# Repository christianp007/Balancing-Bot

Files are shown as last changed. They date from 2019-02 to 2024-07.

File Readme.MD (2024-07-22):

# Balancing-Bot
 A 3d printable balancing bot designed in Fusion360

Just another balancing robot... but with hair! :-)

The bot is using stepper motors, an accelerometer/gyro and a pid loop programmed in Arduino IDE for an AtMega328p.<br>
The bot can be controlled using a Bluetooth, i recommend the app 'Arduino Bluetooth RC Car' for Android (not tested with IPhone).

The source code and build instructions (german language only at the moment) are included in a PDF: [Build Instruktions](Balancing%20Bot%20instructions.pdf)<br>

Programming the HC-05 module with these instructions:<br>
(from https://www.instructables.com/Modify-The-HC-05-Bluetooth-Module-Defaults-Using-A/)<br>
set serial monitor in arduino ide to 9600 baud and connect<br>
AT+ORGL<br>
AT+VERSION?<br>
AT+NAME=Bot red<br>
AT+UART=57600,1,0<br>
AT+POLAR)1,0<br>

The code is structured this way it is as it was provided incomplete and had to be completed by the teams. Additionally it was my first arduino project (i'm a java programmer)...<br>

It was designed mostly in Fusion 360 and for the skind/hairs OpenSCAD.<br>
Fusion 360 couldn't handle the thousands of hairs, however rendering in openscad can take a few hours.

Bill of materials (BOM):<br>
3x stepper motor 14HS11-1004S (Nema 14 35x25x28mm with low inductance)<br>
3x stepper driver DRV8834 (this is a low voltage driver that works with 5V)<br>
1x Powerbank 'Powerad Slim 2'<br>
1x Bread Board 830 point<br>
1x Microcontroller ATMega328P-PU (preferably with Arduino Bootloader installed)<br>
1x HC-05 Bluetooth module<br>
1x Gyro MPU-9250<br>
1x 5V Speaker<br>
1x Micro USB adapter<br>
1x capacitor 220uF<br>
4x capacitor 100uF<br>
1x capacitor 10uF<br>
2x capacitor 10pF<br>
4x resistor 1 kOhm<br>
4x resistor 10 kOhm<br>
1x Pushbutton<br>
1x crystal 16 MHz<br>
(optional) Bluetooth Stick for your computer (upload Arduino sketches directly from arduino ide)<br>
some breadboard wires or cut and strip wires yourself<br>

Print Time: About 24 hours<br>
I used an Kossel XL and a 0.25mm nozzle<br>

Material: PLA<br>
The tire have to be printed in a flexible material (i used Ninjaflex), or you can print tires and wheels as one part in PLA.

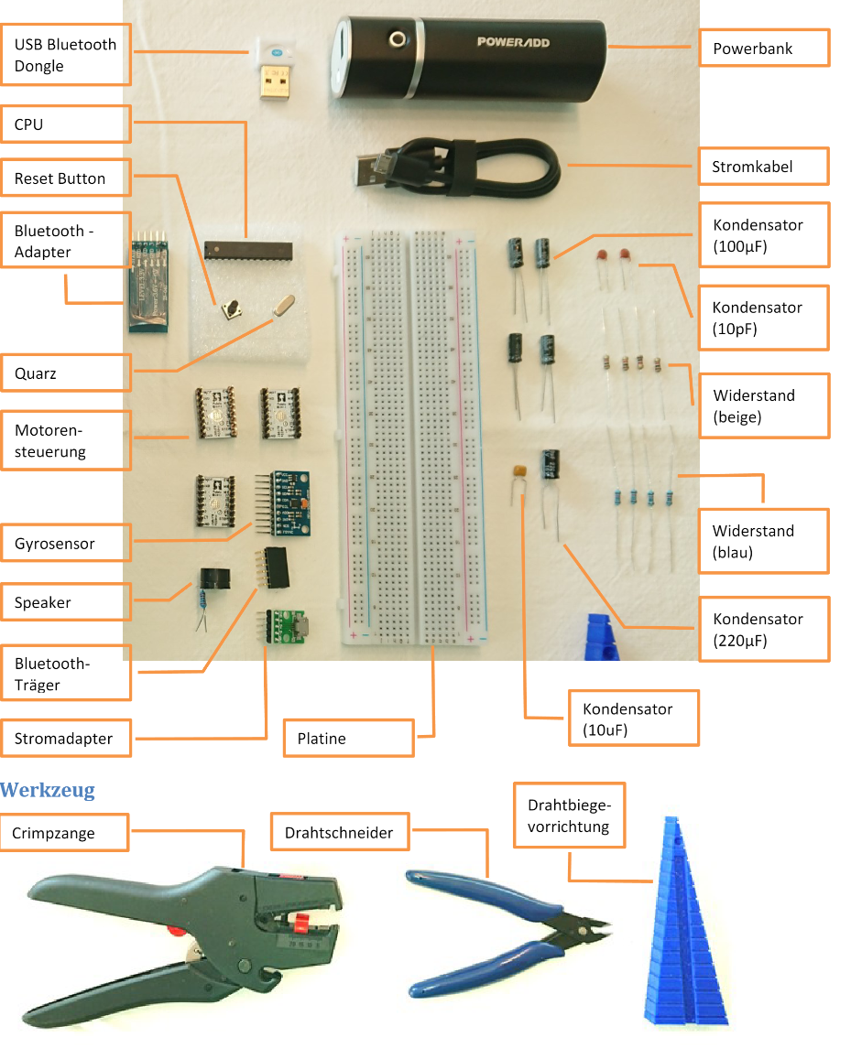
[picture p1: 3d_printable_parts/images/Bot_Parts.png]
Bot_Parts Bot Parts

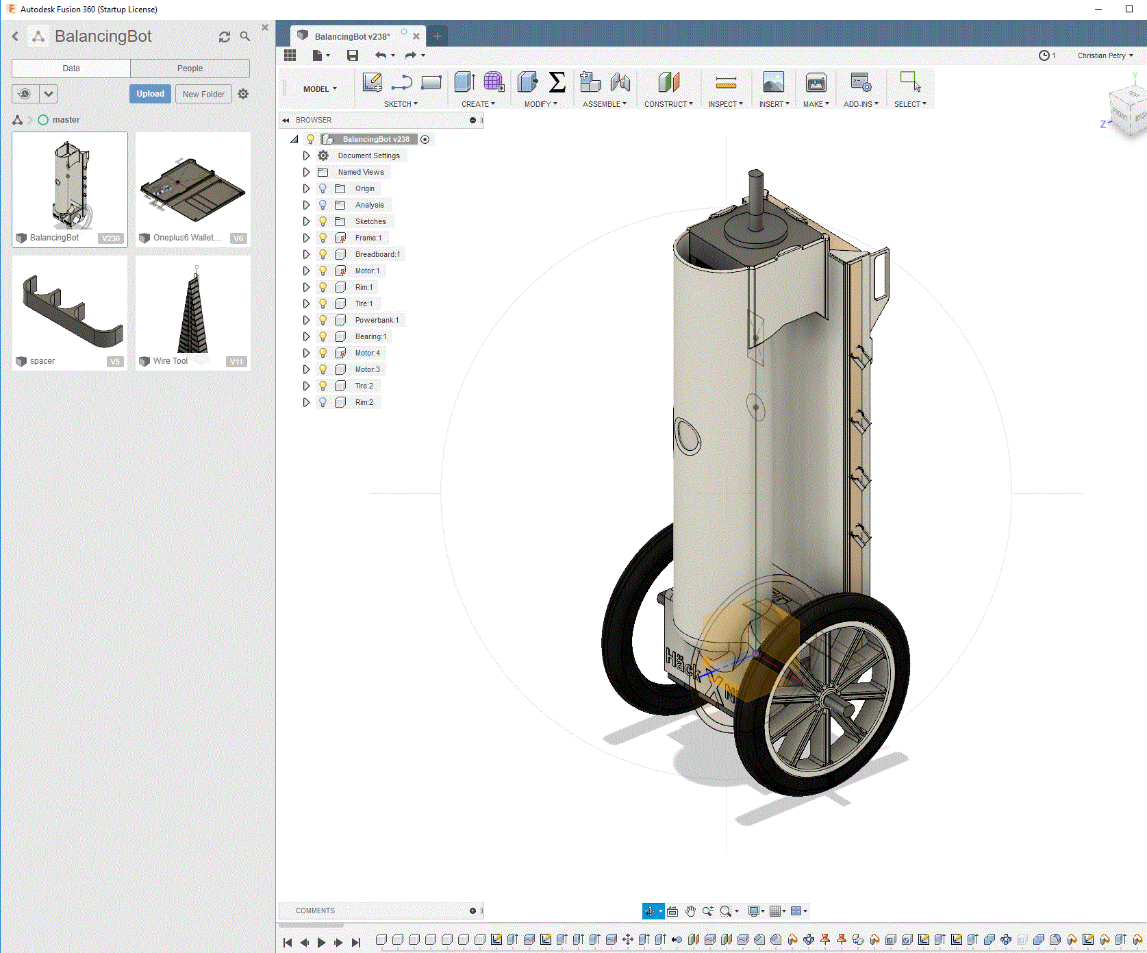
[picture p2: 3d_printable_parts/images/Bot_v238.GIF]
Bot_v238 Bot v238

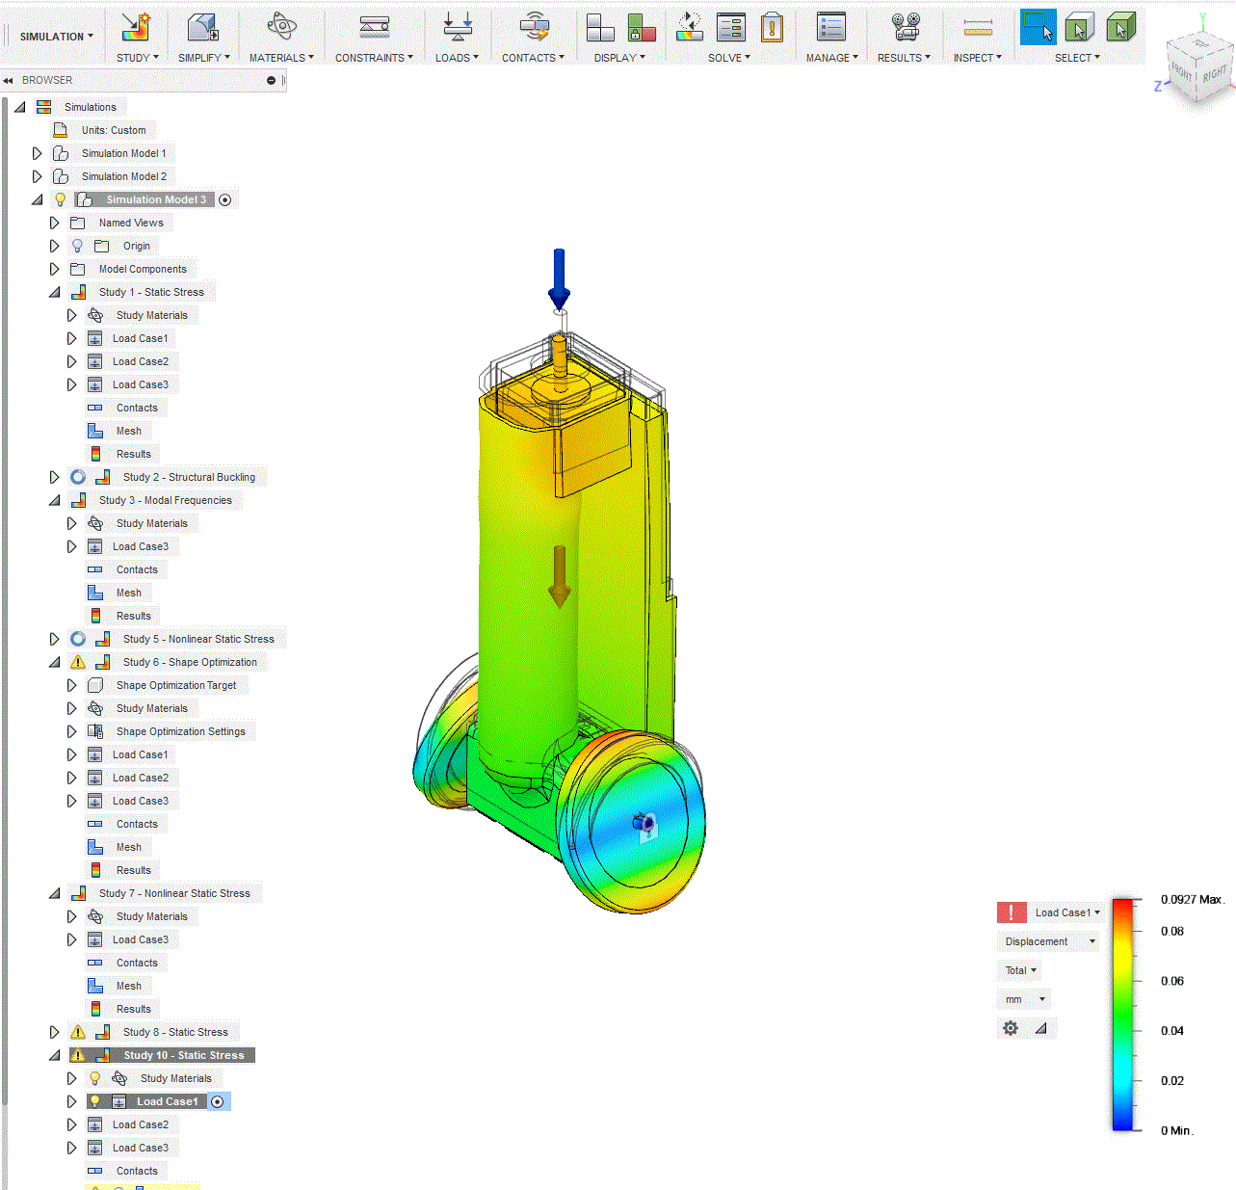
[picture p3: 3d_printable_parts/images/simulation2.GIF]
simulation2

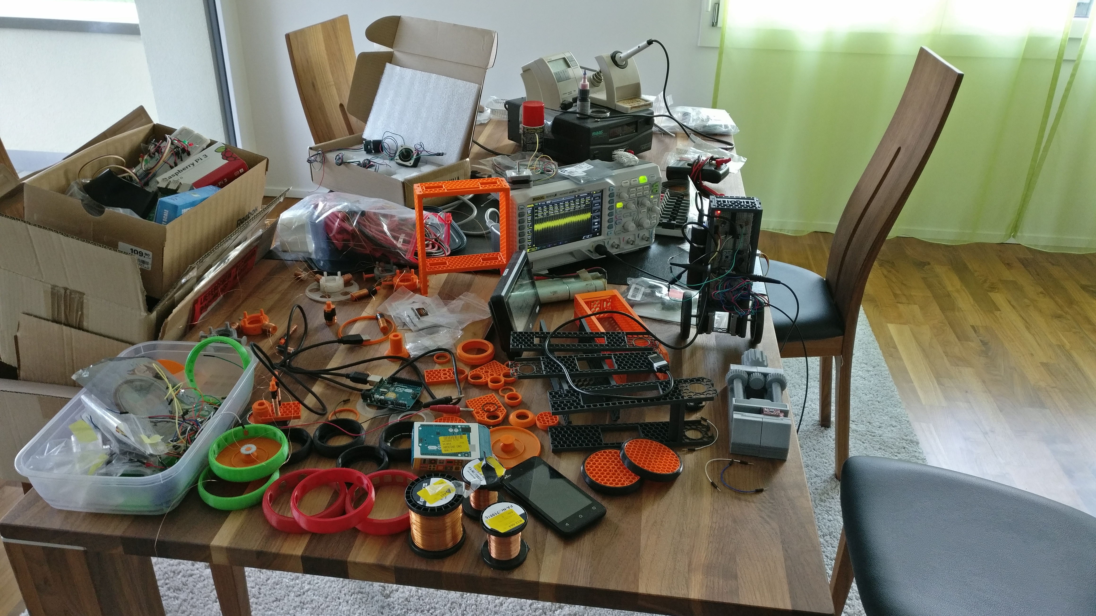
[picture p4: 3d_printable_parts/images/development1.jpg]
development1

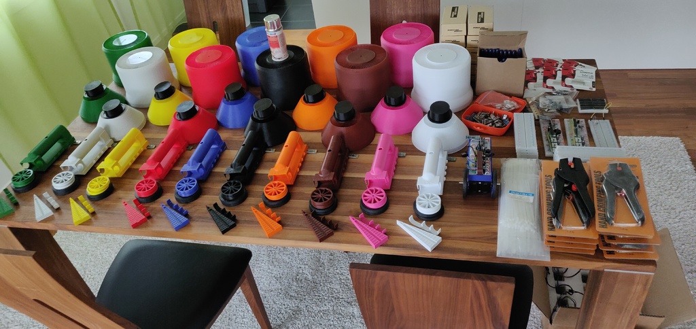
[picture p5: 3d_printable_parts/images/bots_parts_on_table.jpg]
bots_parts_on_table

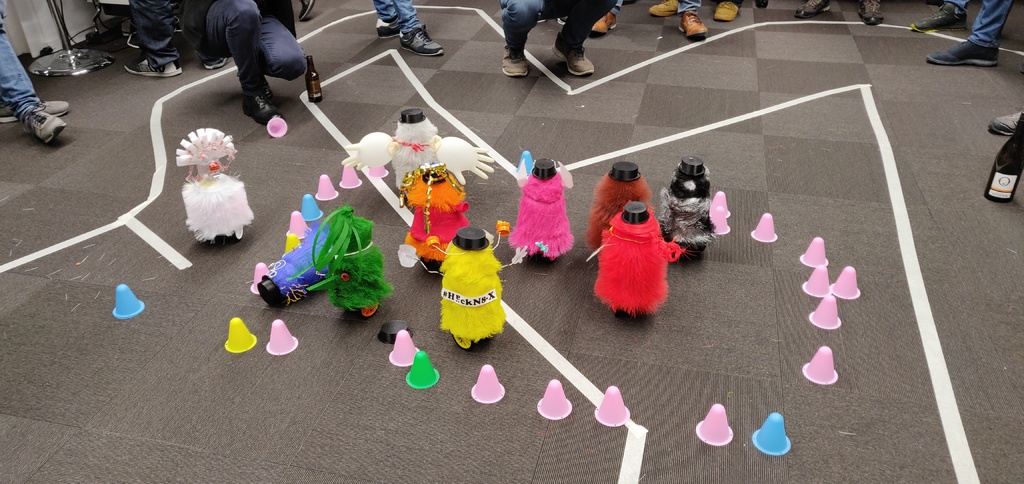
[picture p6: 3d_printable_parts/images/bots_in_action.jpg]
bots_in_action

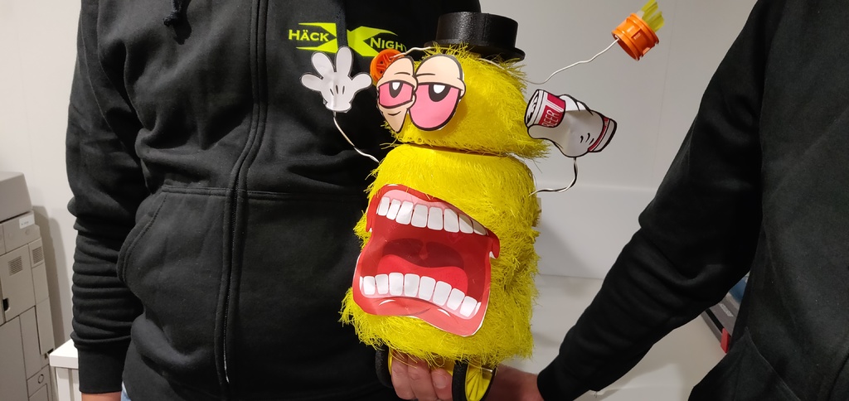
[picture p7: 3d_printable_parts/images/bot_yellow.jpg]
bot_yellow

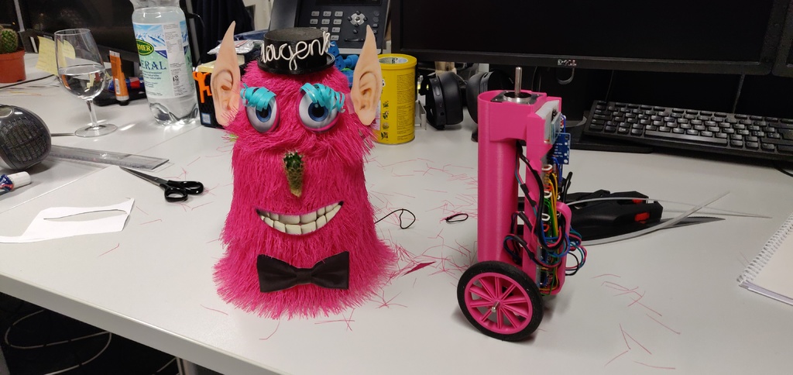
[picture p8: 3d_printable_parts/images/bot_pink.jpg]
bot_pink

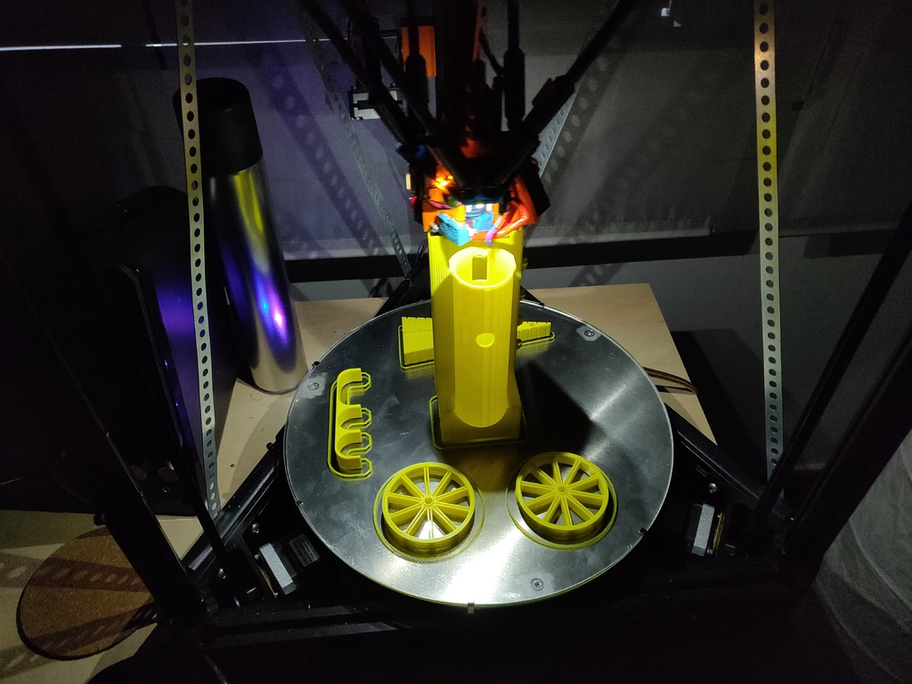
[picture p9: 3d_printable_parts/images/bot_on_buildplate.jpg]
bot_on_buildplate

hair

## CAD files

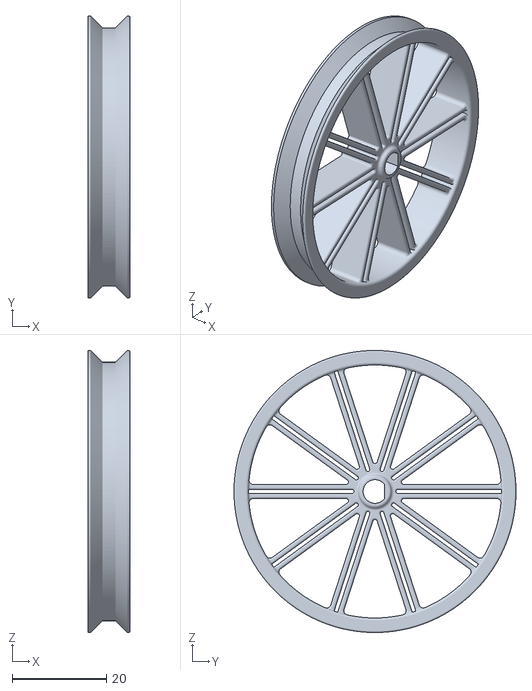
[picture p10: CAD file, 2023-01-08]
3d_printable_parts/RimV238.stl
9.00 x 60.0 x 60.0

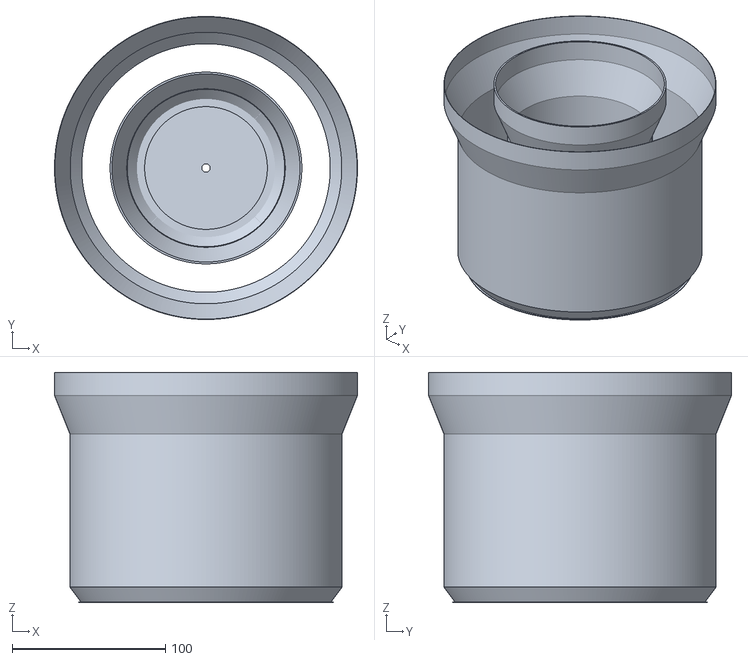
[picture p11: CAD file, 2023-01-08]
3d_printable_parts/balancing_bot_suiteV3__skin.stl
197.5 x 197.5 x 150.0

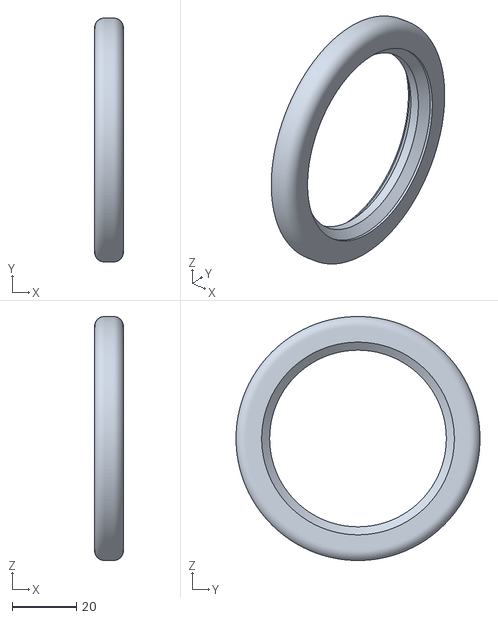
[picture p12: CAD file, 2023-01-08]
3d_printable_parts/TireV238.stl
9.00 x 76.0 x 76.0

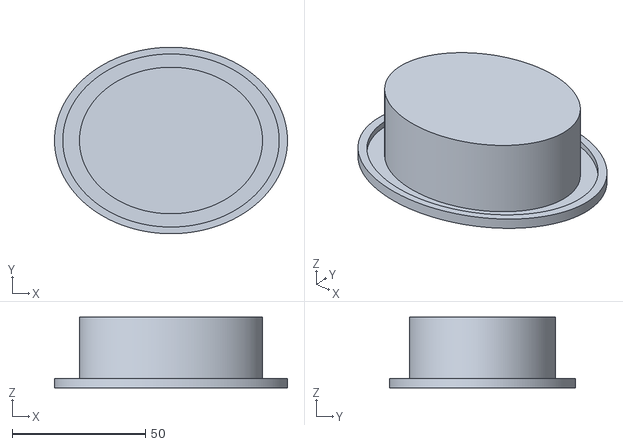
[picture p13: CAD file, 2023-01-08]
3d_printable_parts/balancing_bot_suiteV3__hat.stl
87.5 x 70.0 x 26.5

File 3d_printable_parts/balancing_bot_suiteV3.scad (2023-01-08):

OVERLAP = 0.001;
HAIRS_PER_LAYER = 100;
LAYER_SHIFT_DISTANCE = 0.2;

defaultHairLength = 36;
nozzleWidth = 0.27;
layerHeight = 0.20;
innerOverlap = 2.0*nozzleWidth;
outerOverlap = 0.5*nozzleWidth;
defaultWallThickness = 3*nozzleWidth;
topThickness = 4*layerHeight;

PART = "HAT"; // BODY_HAIR, BODY_SKIN, HEAD_HAIR, HEAD_SKIN, HAT

create();

module create(){
    if (PART == "BODY_HAIR"){
        $fn=50;
        hair(90,105,10,0);
        hair(105,105,5,10);
        hair(105,105,95,15);
        hair(105,125,25,110);
        hair(125,125,15,135);
    } else if (PART == "BODY_SKIN"){
        $fn=200;
        skin(90,105,10,0,1.5*defaultWallThickness);
        skin(105,105,5,10,1.5*defaultWallThickness);
        skin(105,105,95,15);
        skin(105,125,25,110);
        skin(125,125,15,135,1.5*defaultWallThickness);
        difference(){
            cylinder(d=90+OVERLAP, h=topThickness);
            translate([0,0,-OVERLAP/2])
            cylinder(d=5.5, h=topThickness+OVERLAP);
        }
        translate([0,0,topThickness])
        difference(){
            cylinder(d=90+OVERLAP, h=topThickness);
            translate([0,0,-OVERLAP/2])
            cylinder(d=80, h=topThickness+OVERLAP);
        }
        
        difference(){
            cylinder(d=90+2*defaultHairLength+4, h=2*layerHeight);
            translate([0,0,-OVERLAP/2])
            cylinder(d=90+2*defaultHairLength, h=2*layerHeight+OVERLAP);
        }
    } else if (PART == "HEAD_HAIR"){
        $fn=50;
        headDia = 91;
        hair(headDia,headDia,15,0);
        hair(headDia,20,headDia*1.15/2-1,15);
    } else if(PART == "HEAD_SKIN"){
        $fn=200;
        headDia = 91;
        
        difference(){
            union(){
                translate([0,0,15])
                scale([1,1,1.15])
                difference(){
                    sphere(headDia/2);
                    translate([-headDia/2,-headDia/2,-headDia])
                    cube(headDia+OVERLAP);
                    
                    translate([-headDia/2,-headDia/2,headDia/2-1])
                    cube(headDia+OVERLAP);
                }
                    
                translate([0,0,0])
                cylinder(d=15, h=headDia/2*1.15+15-1.5+24, $fn=6);
                
                cylinder(d=headDia,h=15);
            }
            
            cylinder(d=5.2, h=100, center=true);
            cylinder(d=5.6, h=0.6, center=true);
        }
        
        difference(){
            cylinder(d=90+2*defaultHairLength+4, h=2*layerHeight);
            translate([0,0,-OVERLAP/2])
            cylinder(d=90+2*defaultHairLength, h=2*layerHeight+OVERLAP);
        }
        
        skin(headDia,headDia,15,0);
        skin(headDia,20,headDia*1.15/2-1.2,15);
    } else if (PART == "HAT"){
        $fn=200;
        difference(){
            scale([1.25,1,1])
            {
                cylinder(d=70, h=1.5);
                
                translate([0,0,1.5-OVERLAP])
                difference(){
                    cylinder(d=70, h=2);
                    cylinder(d=65, h=2+OVERLAP);
                }
                
                translate([0,0,1.5-OVERLAP])
                cylinder(d=55, h=25);
            }
            
            translate([0,0,0])
            cylinder(d=15.9, h=25.2, $fn=6);
            
            translate([0,0,0])
            cylinder(d=16.2, h=0.8, $fn=6);
            
            translate([0,0,-OVERLAP])
            cylinder(d=16.5, h=0.4, $fn=6);
        }
    }
}

module hair(innerDiaStart, innerDiaEnd, height, startHeight, hairLength=defaultHairLength, layerShiftStart=0, wallThickness=defaultWallThickness){
    color("blue")    
    for(i=[1:height]){
        dia = innerDiaStart - 2*innerOverlap + (innerDiaEnd-innerDiaStart)*i/height;
        for (j=[0:360/HAIRS_PER_LAYER:359.9]){
            rotate([0,0,j+(layerShiftStart+i*360/HAIRS_PER_LAYER*LAYER_SHIFT_DISTANCE)])
            translate([dia/2,-nozzleWidth/2,startHeight+i])
            cube([hairLength+innerOverlap+outerOverlap,nozzleWidth,layerHeight]);
            //rotate([-90,0,90])
            //cylinder(h=hairLength,d=nozzleWidth,center=true);
        }
    }
}

module skin(innerDiaStart, innerDiaEnd, height, startHeight, wallThickness=defaultWallThickness){
    translate([0,0,startHeight])
    difference(){
        cylinder(d1=innerDiaStart, d2=innerDiaEnd, h=height);
        translate([0,0,-OVERLAP/2])
        cylinder(d1=innerDiaStart-2*wallThickness, d2=
innerDiaEnd-2*wallThickness, h=height+OVERLAP);
    }
    
    translate([0,0,startHeight])
    difference(){
        cylinder(d1=innerDiaStart+2*defaultHairLength+2*nozzleWidth, d2=innerDiaEnd+2*defaultHairLength+2*nozzleWidth, h=height);
        translate([0,0,-OVERLAP/2])
        cylinder(d1=innerDiaStart+2*defaultHairLength, d2=
innerDiaEnd+2*defaultHairLength, h=height+OVERLAP);
    }
}

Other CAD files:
3d_printable_parts/spacer v5.f3d

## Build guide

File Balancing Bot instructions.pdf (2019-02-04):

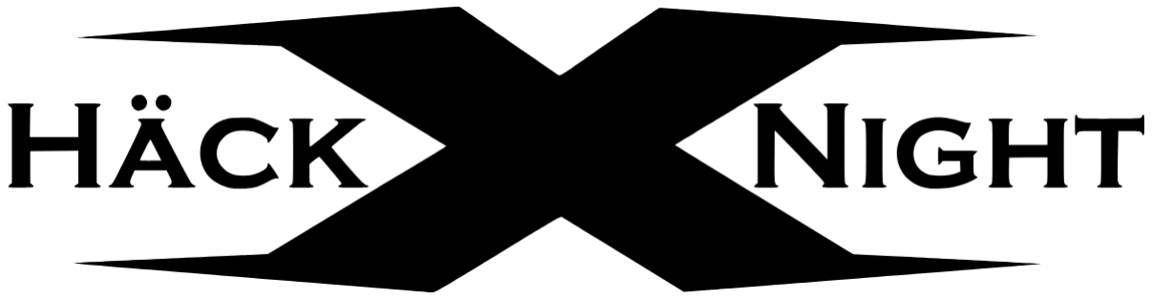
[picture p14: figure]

# Bauanleitung Balancing Bot

### Tipps zum Zusammenbau / Best practices

- Benutze die Drahtbiegevorrichtung, um die (meisten) Drähte auf die gewünschte Länge zu biegen und zu schneiden. Für die längeren Drähte brauchst du ein Lineal.
- Benutze die Drahtbiegevorrichtung auch zum Kürzen von Kondensatoren und Widerständen (in die Vertiefung im oberen Teil einsetzen und auf der Rückseite abschneiden).
- Spare Zeit, indem dein Team gleichzeitig die Drähte vorbereitet und die elektrischen Komponenten auf der Platine installiert.
- Lese jeden Schritt in dieser Anleitung sorgfältig durch. Achte insbesondere auf die korrekte Polung und vergleiche deine Arbeit mit den Bildern.
- Lasse nach jedem Arbeitsschritt die Platine durch eine zweite Person reviewen. Fehlerhafte Verbindungen sind im Nachhinein extrem schwierig zu finden!
- Keine Kabel und Komponenten ein- oder ausstecken, wenn die PowerBank angeschlossen ist! PowerBank immer vorher trennen!

### Übersicht

### Bot Bauteile

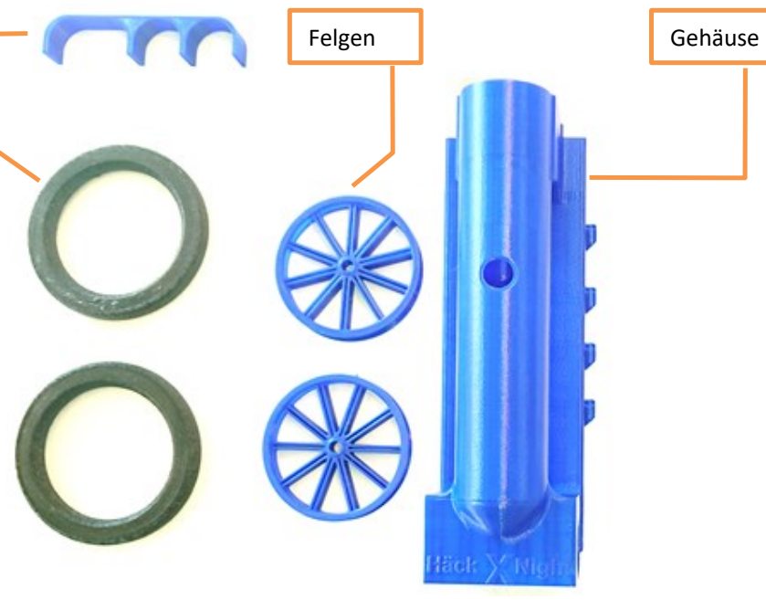
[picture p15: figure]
Felgen; Gehäuse

Schutzkappe

Reifen

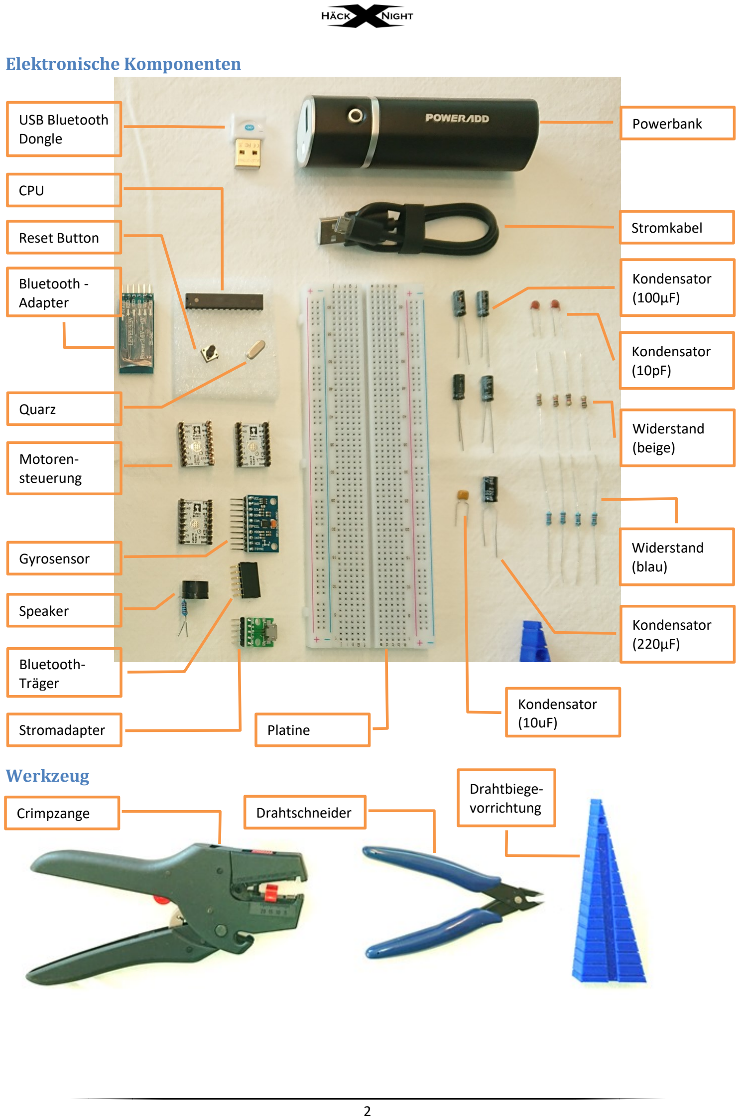
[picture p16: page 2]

### Elektronische Komponenten

### Werkzeug

USB Bluetooth
Dongle

Powerbank

CPU

Reset Button

Bluetooth -
Adapter

Stromkabel

Quarz

Motorensteuerung

Gyrosensor

Speaker

Kondensator
(100µF)

Kondensator
(10pF)

Widerstand
(beige)

Widerstand
(blau)

Kondensator
(220µF)
Bluetooth-Träger
Stromadapter | Platine

Kondensator
(10uF)
Crimpzange | Drahtschneider

Drahtbiegevorrichtung

### Vorbereitung

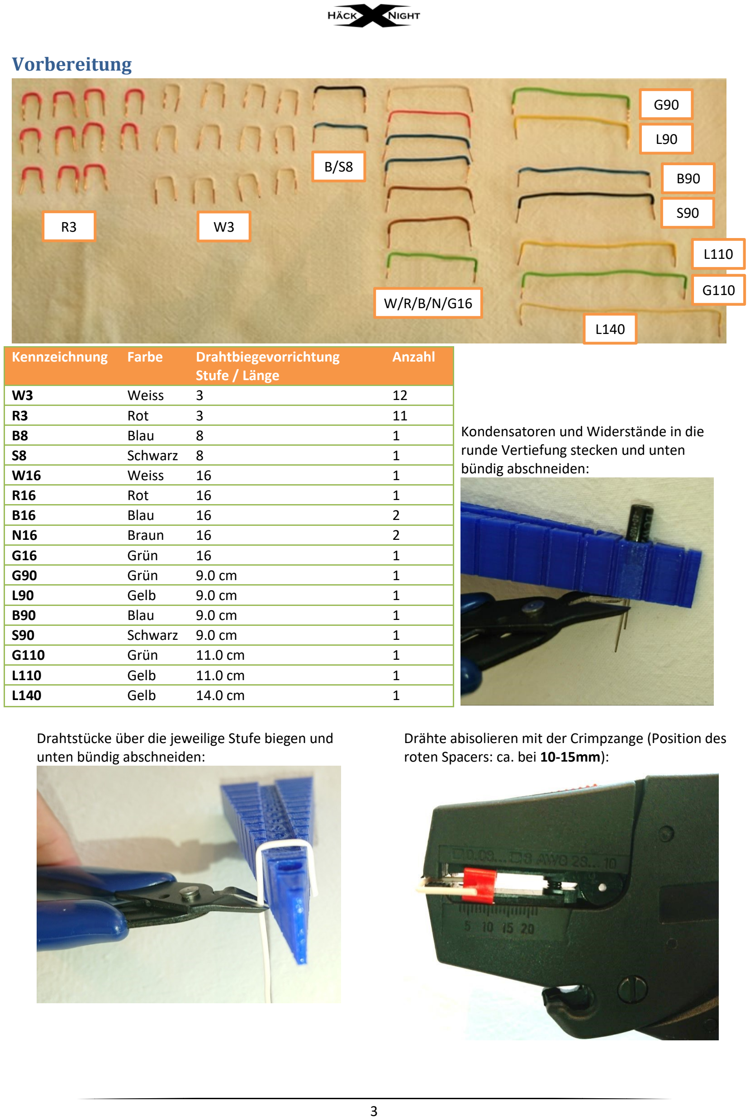
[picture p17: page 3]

Kennzeichnung | Farbe | Drahtbiegevorrichtung Stufe / Länge

Anzahl

Kondensatoren und Widerstände in die runde Vertiefung stecken und unten bündig abschneiden:

W3 | Weiss | 3 | 12
R3 | Rot | 3 | 11
B8 | Blau | 8 | 1
S8 | Schwarz 8 | 1
W16 | Weiss | 16 | 1
R16 | Rot | 16 | 1
B16 | Blau | 16 | 2
N16 | Braun | 16 | 2
G16 | Grün | 16 | 1
G90 | Grün | 9.0 cm | 1
L90 | Gelb | 9.0 cm | 1
B90 | Blau | 9.0 cm | 1
S90 | Schwarz 9.0 cm | 1
G110 | Grün | 11.0 cm | 1
L110 | Gelb | 11.0 cm | 1
L140 | Gelb | 14.0 cm | 1

Drahtstücke über die jeweilige Stufe biegen und
unten bündig abschneiden:
| | | Drähte abisolieren mit der Crimpzange (Position des roten Spacers: ca. bei 10-15mm):
R3 | W3

B/S8

W/R/B/N/G16

G90

L90

B90

S90

L110

G110

L140

### Bauanleitung

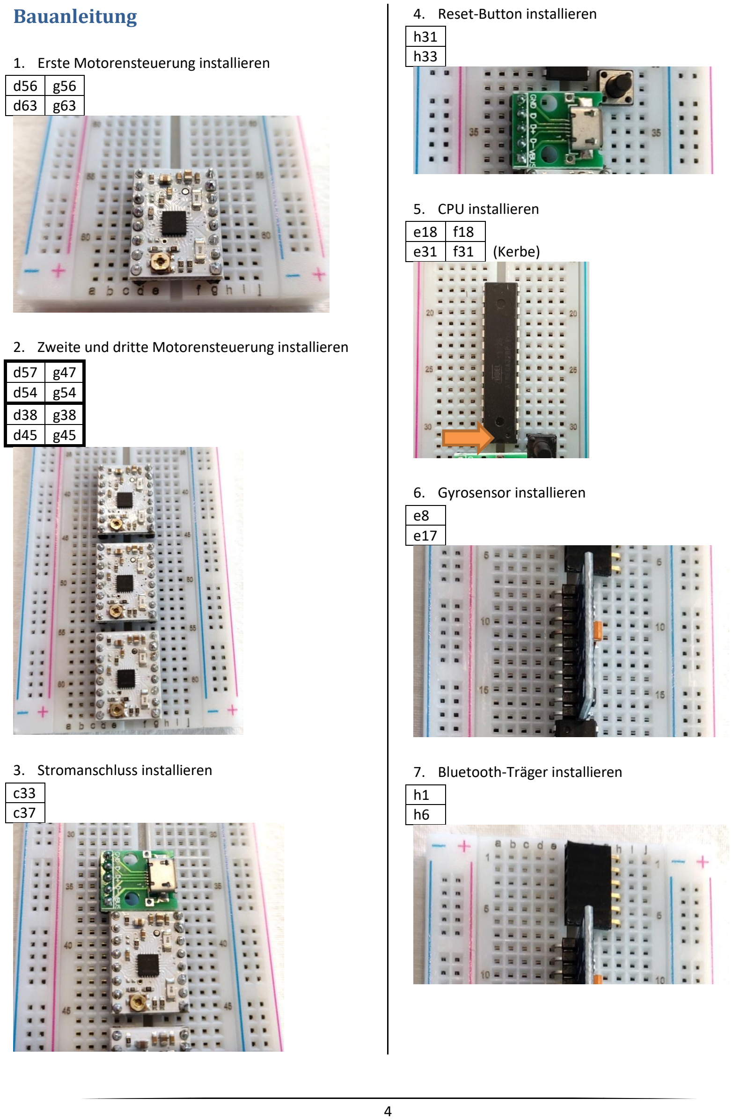
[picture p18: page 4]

1. Erste Motorensteuerung installieren
d56 | g56
d63 | g63
2. Zweite und dritte Motorensteuerung installieren
d57 | g47
d54 | g54
d38 | g38
d45 | g45
3. Stromanschluss installieren c33
c37
4. Reset-Button installieren h31
h33
5. CPU installieren
e18 | f18
e31 | f31 | (Kerbe)
6. Gyrosensor installieren e8
e17
7. Bluetooth-Träger installieren h1
h6

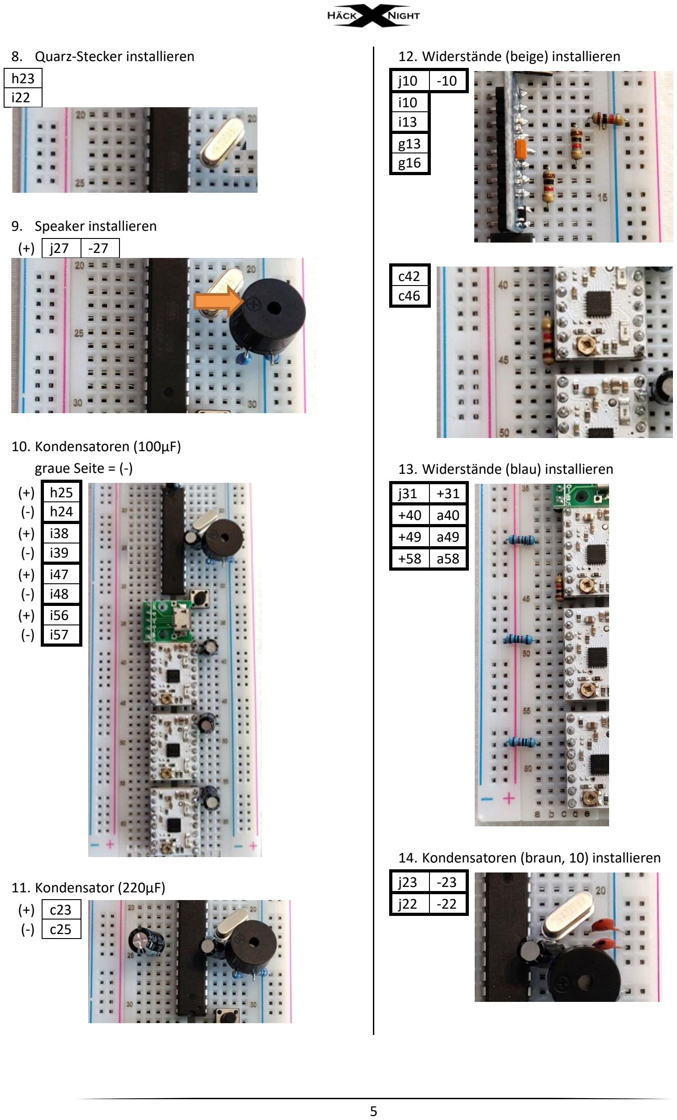
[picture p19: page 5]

8. Quarz-Stecker installieren h23
i22
9. Speaker installieren
(+) | j27 | -27
10. Kondensatoren (100µF)
graue Seite = (-)
(+) | h25
(-) | h24
(+) | i38
(-) | i39
(+) | i47
(-) | i48
(+) | i56
(-) | i57
11. Kondensator (220µF)
(+) | c23
(-) | c25
12. Widerstände (beige) installieren j10 -10
i10
i13
g13
g16

c42
c46
13. Widerstände (blau) installieren
j31 | +31
+40 | a40
+49 | a49
+58 | a58
14. Kondensatoren (braun, 10) installieren
j23 | -23
j22 | -22

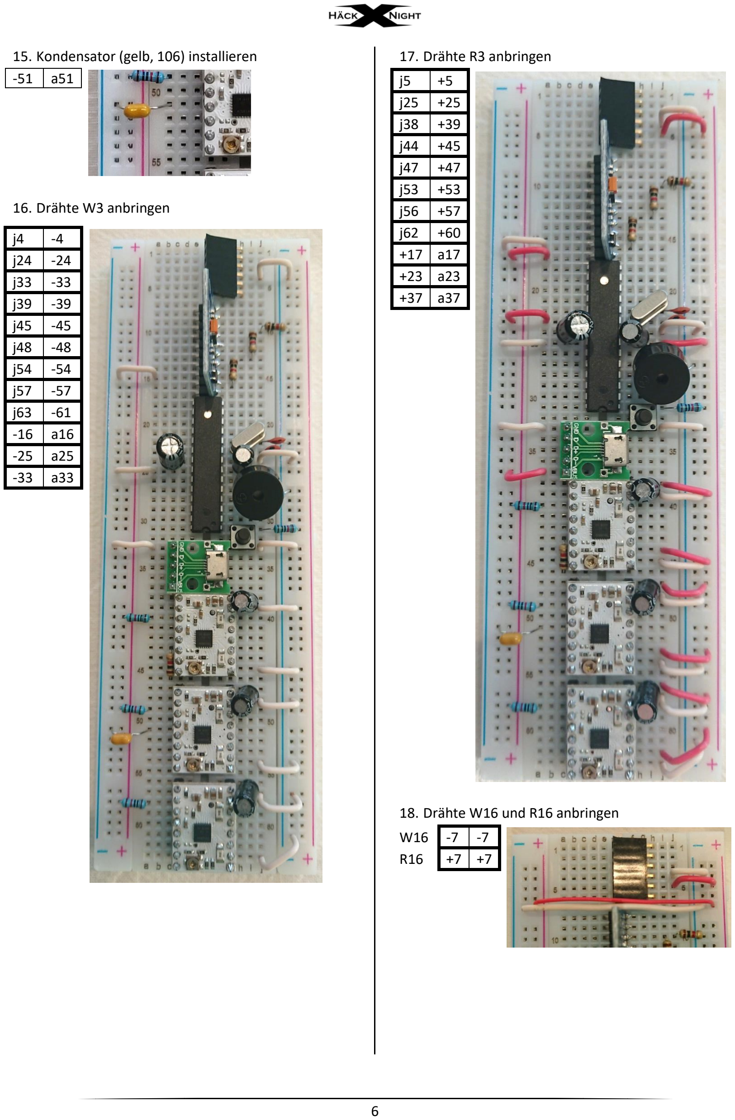
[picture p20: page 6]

15. Kondensator (gelb, 106) installieren -51 a51
16. Drähte W3 anbringen
17. Drähte R3 anbringen
j5 | +5
j25 | +25
j38 | +39
j44 | +45
j47 | +47
j53 | +53
j56 | +57
j62 | +60
+17 | a17
+23 | a23
+37 | a37
18. Drähte W16 und R16 anbringen
W16 | -7 | -7
R16 | +7 | +7
j4 | -4
j24 | -24
j33 | -33
j39 | -39
j45 | -45
j48 | -48
j54 | -54
j57 | -57
j63 | -61
-16 | a16
-25 | a25
-33 | a33

19. Draht S8 anbringen
i2
h13

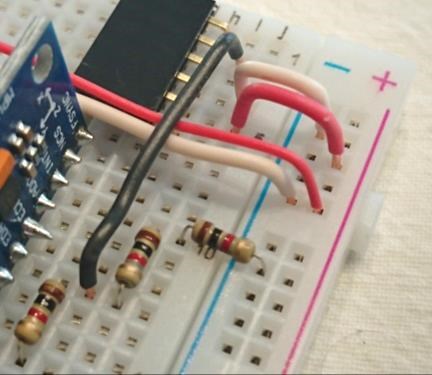
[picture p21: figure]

20. Draht B90 anbringen
(evtl. Speaker dafür entfernen) i3
j30

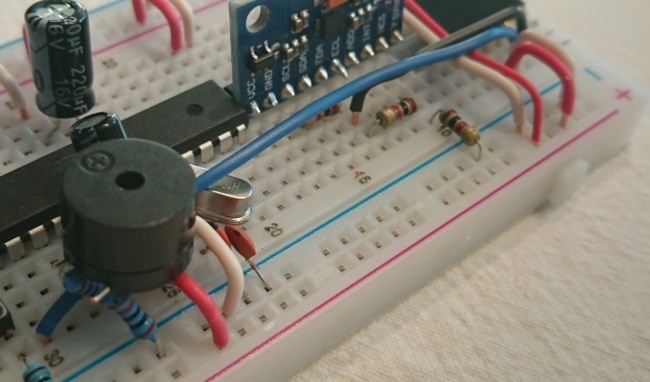
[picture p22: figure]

21. Drähte N16 anbringen
d14 | h16
d30 | g29

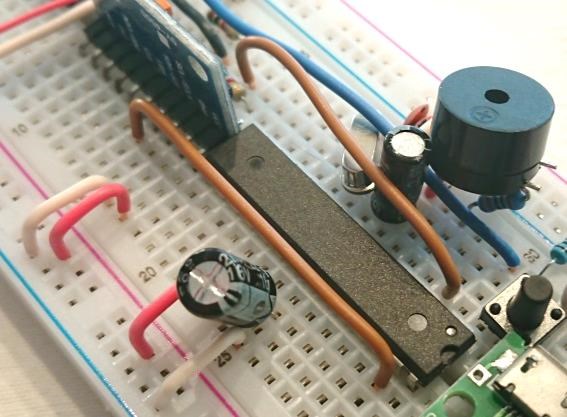
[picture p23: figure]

22. Drähte B16 anbringen
23. Draht B8 anbringen
24. Draht S90 anbringen
b18
b46

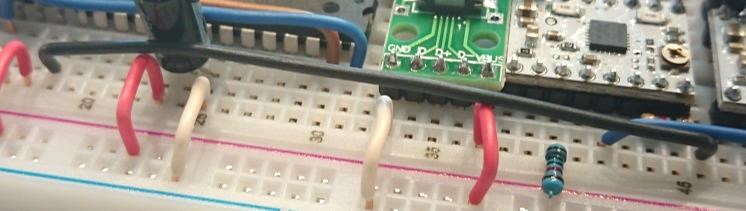
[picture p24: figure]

25. Drähte L90 / L110 / L140 anbringen L90 L110 L140
b20 | b21 | b22
b44 | b53 | b62

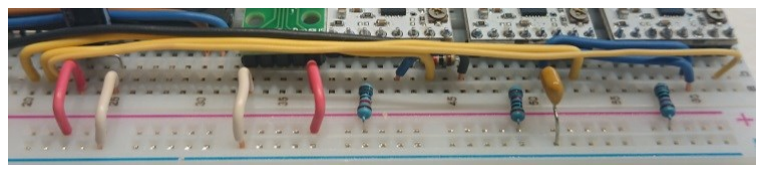
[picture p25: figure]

26. Drähte G16 / G90 / G110 anbringen G16 G90 G110
a27 | a28 | a29
a45 | a54 | a63

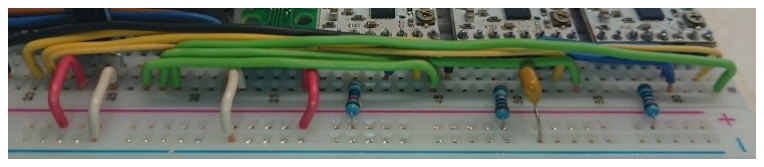
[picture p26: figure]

Die Platine ist nun (vorerst) fertig und bereit für den Einbau in den Bot! Ach ja, der Bot muss ja auch noch vorbereitet werden…

d15 | b42
d31 | a60

b51
b60

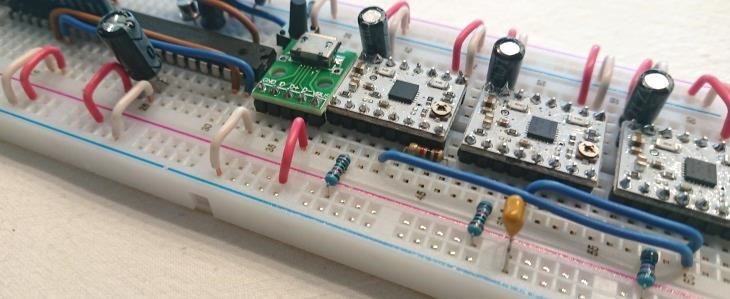
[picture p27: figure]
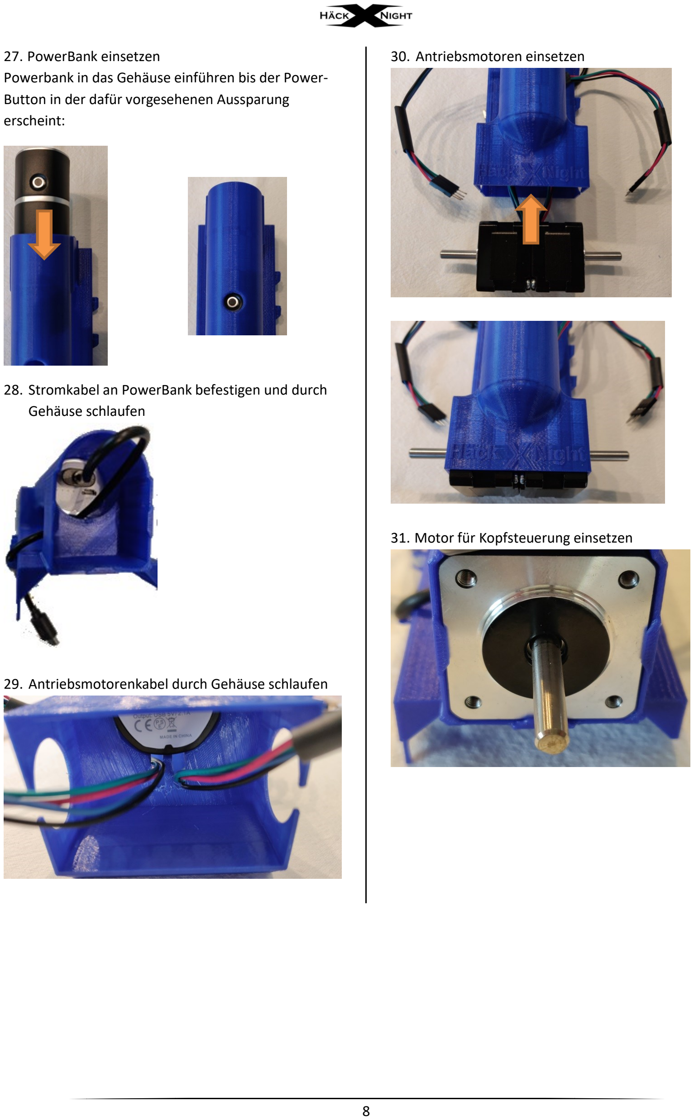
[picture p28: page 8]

27. PowerBank einsetzen
Powerbank in das Gehäuse einführen bis der Power-Button in der dafür vorgesehenen Aussparung erscheint:
28. Stromkabel an PowerBank befestigen und durch Gehäuse schlaufen
29. Antriebsmotorenkabel durch Gehäuse schlaufen
30. Antriebsmotoren einsetzen
31. Motor für Kopfsteuerung einsetzen

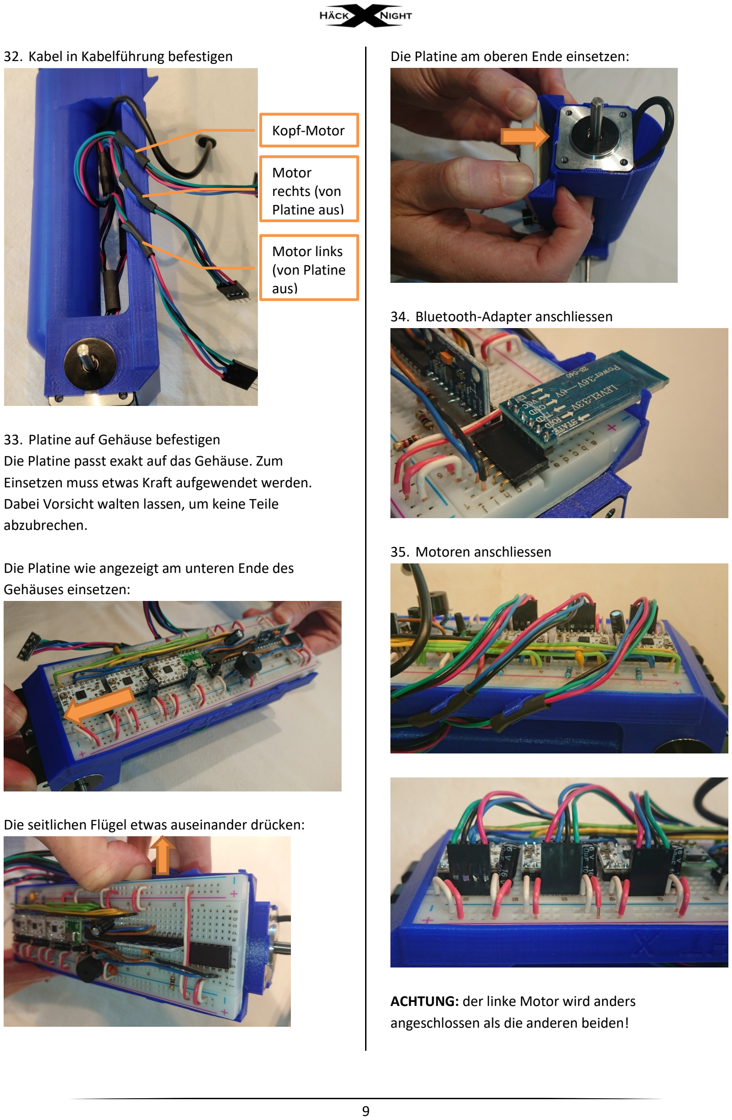
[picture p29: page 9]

32. Kabel in Kabelführung befestigen
33. Platine auf Gehäuse befestigen
Die Platine passt exakt auf das Gehäuse. Zum Einsetzen muss etwas Kraft aufgewendet werden. Dabei Vorsicht walten lassen, um keine Teile abzubrechen.

Die Platine wie angezeigt am unteren Ende des Gehäuses einsetzen:

Die seitlichen Flügel etwas auseinander drücken:

Die Platine am oberen Ende einsetzen:

34. Bluetooth-Adapter anschliessen
35. Motoren anschliessen

ACHTUNG: der linke Motor wird anders angeschlossen als die anderen beiden!

Kopf-Motor

Motor
rechts (von
Platine aus)

Motor links
(von Platine
aus)

36. PowerBank an Stromversorgung anschliessen

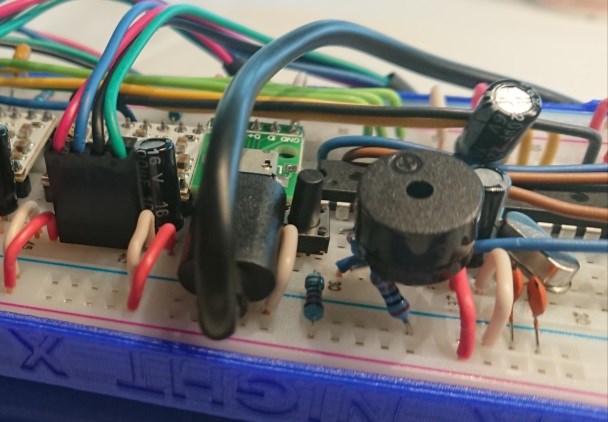
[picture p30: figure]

37. Schutzkappe aufstecken (bissl fummelig)

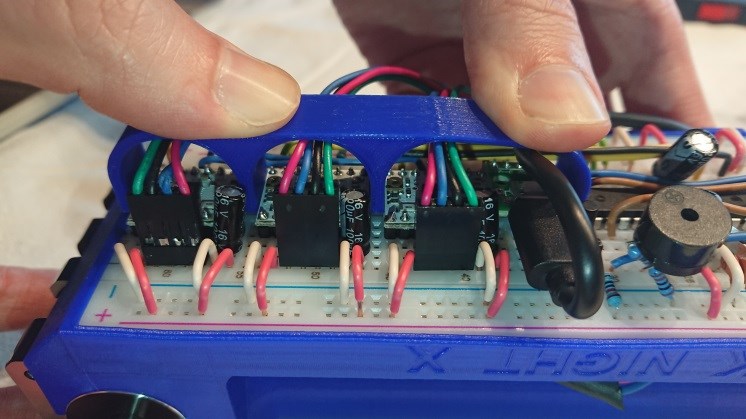
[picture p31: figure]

38. Pneus montieren

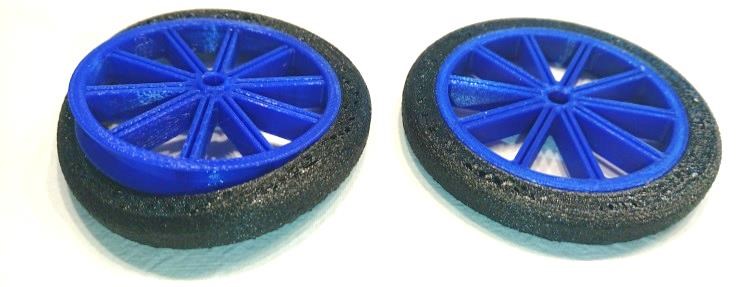
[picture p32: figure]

39. Reifen auf Motorenachsen aufsetzen
Auf zwei Punkte achten:
- Die Achse ist auf einer Seite etwas abgeflacht; ebenso das Loch in den Radspeichen
- Das Rad muss mit der Ausbuchtung nach aussen montiert werden:

Gratulation, ihr habt es geschafft!

Nun noch überprüfen, ob auch alles richtig eingesteckt und verdrahtet ist...

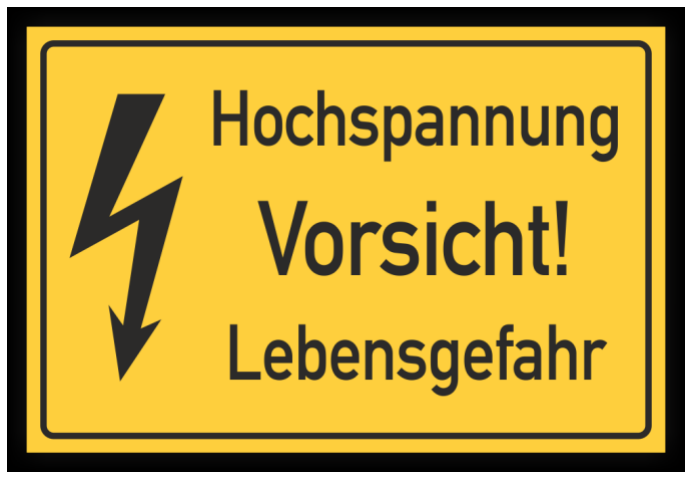
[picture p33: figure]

Keine Kabel und Komponenten ein- oder ausstecken, solange die PowerBank angeschlossen ist!

PowerBank immer vorher ausschalten und ausstecken!

Funktionstest:
1. PowerBank einschalten (ca. 3 Sekunden gedrückt halten. Sobald Bluetooth-Adapter blinkt und Räder etwas blockieren, ist Strom drauf)
2. Willkommens-Musik geniessen
3. Bot senkrecht hinstellen und solange (sanft) fixiert halten bis er von selbst balanciert

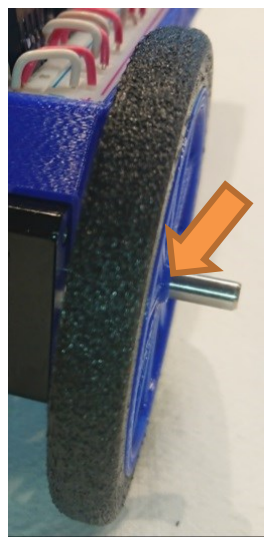
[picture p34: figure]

Wenn der Bot hinfällt oder durchdreht:
- Bot flach auf den Boden legen
- Warten bis er sich beruhigt hat, oder Reset-Button betätigen
- Bot wieder senkrecht hinstellen bis er von selbst balanciert

### Entwicklungsumgebung einrichten

Hinweis: benötigt zwingend eine Windows-Umgebung!

1. USB-Stick an Laptop oder PC anschliessen
2. ArduinoIDE starten von X:\arduino-1.8.7\arduino.exe
3. Tools -> Board -> „Arduino Duemilanove or Diecimila“ auswählen
4. Tools -> Processor -> „ATmega328P“ auswählen
5. Tools -> Programmer -> „AVRISP mkll“ auswählen
6. File -> Preferences -> Show verbose output during: | compilation | upload
7. File -> Open und folgende Datei öffnen: X:\balancingRobotV3\balancingRobotV3.ino
8. Tools -> Port -> angezeigte Ports merken (damit man nachher weiss, welche Ports NICHT zum Bot gehören)
9. Bot einschalten
10. Bluetooth einrichten:
a. Falls auf PC oder Laptop Bluetooth verfügbar ist: Bluetooth aktivieren
b. Falls auf PC oder Laptop kein Bluetooth verfügbar: Bluetooth-Dongle anschliessen
11. Bluetooth Einstellungen öffnen
12. Neues Bluetooth-Gerät hinzufügen und nach Gerät Bot {Color} suchen, wobei {Color} deiner Team-Farbe

entspricht

13. Pin eingeben: 1234

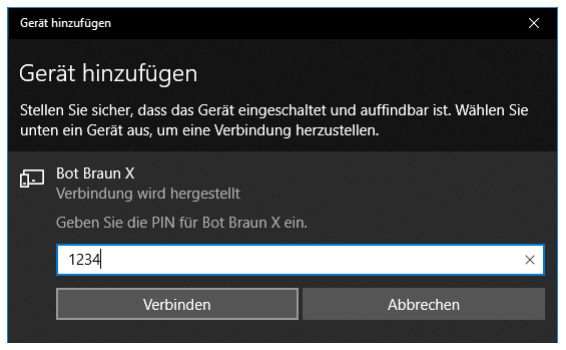
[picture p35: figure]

14. In der ArduinoIDE unter Tools -> Port den neuen Port auswählen. Evtl. IDE dazu neu starten.

Um das Projekt zu kompilieren: Ctrl + R drücken
- Fehler werden in roter Schrift in die Konsole geschrieben; zudem wird der Cursor an die Position des letzten Fehlers gesetzt.

Um das Projekt auf den Bot zu laden:
1. Reset-Button auf Bot gedrückt halten und das blinkende rote Licht am Bluetooth-Modul beobachten.
2. Ctrl + U drücken.
3. Reset-Button solange gedrückt halten, bis das rote Licht am Bluetooth-Modul unregelmässig wird. Dann Reset-Button sofort loslassen.
4. Upload wird durch einen Fortschrittsbalken (###...) in der Konsole angezeigt.
5. Wenn der Upload funktioniert hat, wird die Software auf dem Bot automatisch neu gestartet, und die Startmusik ertönt.

### Smartphone App einrichten

1. App von Google Play Store herunterladen: https://play.google.com/store/apps/details?id=braulio.calle.bluetoothRCcontroller

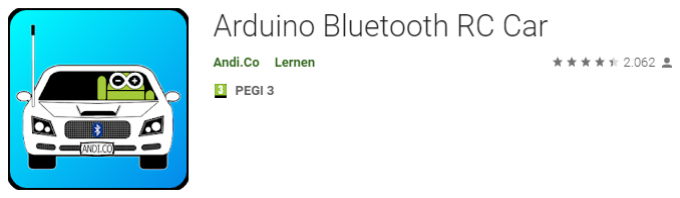
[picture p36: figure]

2. Bluetooth-Kopplung des Bots mit dem PC beenden (Bluetooth auf PC deaktivieren)
3. Bluetooth auf Handy aktivieren und mit Bot {Color} verbinden (Pin: 1234)
4. Wenn die Kopplung erfolgreich war, App starten
5. Einstellungen -> Mit Car verbinden -> Bot {Color} auswählen
6. Sobald das Statuslicht oben links grün leuchtet, kann mit dem Bot herumgekurvt werden (vorausgesetzt, ihr habt die Software auf dem Arduino entsprechend erweitert… )

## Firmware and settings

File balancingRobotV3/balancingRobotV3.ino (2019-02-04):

#include "balancingRobotV3.h"
#include "melody.h"

// --------------------- START custom settings ---------------------
const float INITIAL_TARGET_ANGLE = 2.5; // approximation of the angle at which the bot stands still
const float STARTUP_ANGLE_TOLERANCE = 3.0; // the acceptable range of angle error for start balancing
const float TIPOVER_ANGLE_OFFSET = 35; // stop motors if bot has tipped over
const float MAX_ACCELLERATION = 200.0; // maximum acceleration in steps per second per loop iteration
const float COMPLEMENTARY_FILTER_GYRO_COEFFICIENT = 0.999; // how much to use gyro value compared to accerelometer value
// ---------------------  END custom settings  ---------------------

// --------------------- START PID settings ---------------------
// pid for controlling angle
const float PID_ANGLE_P_GAIN = 6; // proportional pid gain
const float PID_ANGLE_I_GAIN = 0.05; // integral pid gain
const float PID_ANGLE_D_GAIN = -250; // differential pid gain
const float PID_ANGLE_I_MAX = 20; // limit for integral pid
const float PID_ANGLE_D_MAX = 20; // limit for differential pid

// pid for controlling speed
const float PID_SPEED_P_GAIN = 13.0;
const float PID_SPEED_I_GAIN = 0.01;
const float PID_SPEED_D_GAIN = 0;
const float PID_SPEED_I_MAX = 50000;
const float PID_SPEED_D_MAX = 10000;

// pid for controlling position
const float PID_POSITION_P_GAIN = -5;
const float PID_POSITION_I_GAIN = 0;
const float PID_POSITION_D_GAIN = 0;
const float PID_POSITION_I_MAX = 20;
const float PID_POSITION_D_MAX = 20;
// --------------------- END PID settings ---------------------

unsigned long currentTime = millis();

// --------------------- START music variables  ---------------
boolean playMusicModeActive = false;
int lastMusicTone = -1;
unsigned long lastMusicTime = 0;
int *balancing_melody = MELODY_PIRATE_CARIBBEAN;
int balancing_melody_size = sizeof(MELODY_PIRATE_CARIBBEAN)/sizeof(int);
// ---------------------- END music variables  ----------------

int count = 0;
void debugLoop(){
  if (count++ >= 50){
    count = 0;
    debugOutput();
  }
}

void debugOutput(){
    /* Use this to debug! 
     * don't do any computational intesive stuff as this will affect the balancing
     */
    //Serial.println(bodySpeed);
  
}

void serialRead(){  
  //serialReadPosition();
  serialReadDirection();
}

boolean getAccelGyro = true;
void loop() {
  currentTime = millis();
  setPowerLimit();
  debugLoop();
  serialRead();

  if (playMusicModeActive){
    playMusic();
  }

  if (!enable) {
    waitForTargetAngle();
  }

  // every other iteration either read new accelgyro data or step motors
  getAccelGyro = !getAccelGyro;
  if (getAccelGyro){
    getAccelGyroData();
    calculatePitch();

    if (abs(pitch - INITIAL_TARGET_ANGLE) > TIPOVER_ANGLE_OFFSET) {
      disableBot();
      return;
    }
  } else {
    if (mode >= POSITION_MODE){
      pid_position_output_motor1 = calculatePidPosition(pid_position_setpoint_motor1, pid_position_i_motor1, pid_position_error_motor1, motor_steps[MOTOR_RIGHT_ID]);
      pid_position_output_motor2 = calculatePidPosition(pid_position_setpoint_motor2, pid_position_i_motor2, pid_position_error_motor2, motor_steps[MOTOR_LEFT_ID]);
      calculatePidSpeedSetpoint();
    }
  
    calculateBodySpeed();
    pid_speed_output_motor1 = calculatePidSpeed(pid_speed_setpoint, pid_speed_i_motor1, pid_speed_error_motor1);
    pid_speed_output_motor2 = calculatePidSpeed(pid_speed_setpoint, pid_speed_i_motor2, pid_speed_error_motor2);
  
    calculatePidAngleSetpoint();
    pid_angle_output_motor1 = calculatePidAngle(pid_angle_setpoint_motor1, pid_angle_i_motor1, pid_angle_error_motor1);
    pid_angle_output_motor2 = calculatePidAngle(pid_angle_setpoint_motor2, pid_angle_i_motor2, pid_angle_error_motor2);
  }

  int stepCount_motor1 = calculateStepCount(pid_angle_output_motor1, stepsPerSecond_motor1, partialSteps_motor1, motor_step_iteration_interval, +rotation_speed_setpoint/2.0, MAX_ACCELLERATION);
  int stepCount_motor2 = calculateStepCount(pid_angle_output_motor2, stepsPerSecond_motor2, partialSteps_motor2, motor_step_iteration_interval, -rotation_speed_setpoint/2.0, MAX_ACCELLERATION);
  int stepCount_motor3 = head_rotation_speed_setpoint*5.0;
  
  /*if (abs(stepCount_motor1) > 2*MICROSTEPPING || abs(stepCount_motor2) > 2*MICROSTEPPING){
    playWarningTone(400);
  } else if (abs(stepCount_motor1) > 1.5*MICROSTEPPING || abs(stepCount_motor2) > 1.5*MICROSTEPPING){
    playWarningTone(300);
  } else if (abs(stepCount_motor1) > MICROSTEPPING || abs(stepCount_motor2) > MICROSTEPPING){
    playWarningTone(200);
  }*/

  stepMotors(stepCount_motor1,stepCount_motor2,stepCount_motor3);
}

void serialReadDirection() {
  if (Serial.available() > 0) {
     lastDirectionInput = millis();
     mode = SPEED_MODE;
  
     char c = Serial.read();
     boolean validInput = true;

     switch (c){
      case 'F': forward(); break;
      case 'B': backward(); break;
      case 'L': left(); break;
      case 'R': right(); break;
      case 'G': forward_left(); break;
      case 'I': forward_right(); break;
      case 'H': backward_left(); break;
      case 'J': backward_right(); break;
      case 'V': horn(); break;
      case 'v': /* Horn off */ break;
      case 'X': playMusicModeActive= true; break;
      case 'x': playMusicModeActive= false; break;
      case 'W': head_left(); break;
      case 'w': head_stop(); break;
      case 'U': head_right(); break;
      case 'u': head_stop(); break;
      case 'D': stop(); break;
      case 'S': stop(); break;
      case '0': stop(); break;
      case '1': speed(1); break;
      case '2': speed(2); break;
      case '3': speed(3); break;
      case '4': speed(4); break;
      case '5': speed(5); break;
      case '6': speed(6); break;
      case '7': speed(7); break;
      case '8': speed(8); break;
      case '9': speed(9); break;
      case 'q': speed(10); break;
      default: validInput = false;
     }

     if (validInput){
        target_speed *= MAX_STEPS_PER_SECOND * max_body_speed_factor;
        target_rotation_speed *= MAX_STEPS_PER_SECOND * max_body_speed_factor;
     }
  } else {
    if (millis() - lastDirectionInput > 2000){
      stopSpeedRemoteControl();
    }
  }

  if (mode == SPEED_MODE){
    rampupDirectionControl();
  }
}

void forward(){
  target_speed = 1; target_rotation_speed = 0;
}

void backward(){
  target_speed = -1; target_rotation_speed = 0;
}

void left(){
  target_speed = 0; target_rotation_speed = -0.8;
}

void head_left(){
  target_speed = 0; target_head_rotation_speed = -0.8;
}

void right(){
  target_speed = 0; target_rotation_speed = 0.8; 
}

void head_right(){
  target_speed = 0; target_head_rotation_speed = 0.8;
}

void forward_left(){
  target_speed = 1.0; target_rotation_speed = -0.4;
}

void forward_right(){
  target_speed = 1.0; target_rotation_speed = 0.4;
}

void backward_left(){
  target_speed = -1.0; target_rotation_speed = 0.4;
}

void backward_right(){
  target_speed = -1.0; target_rotation_speed = -0.4;
}

void stop(){
  target_speed = 0; target_rotation_speed = 0;
}

void head_stop(){
  target_speed = 0; target_head_rotation_speed = 0;
}

void speed(int value){
  max_body_speed_factor = value/10.0 * MAX_BODY_SPEED_FACTOR_LIMIT;
}

void horn(){
  playWarningToneWithDuration(250,750);
}

void playMusic(){
  if (lastMusicTone >= balancing_melody_size){
    lastMusicTone = -1;
  }
  
  if (lastMusicTone < 0){
    lastMusicTone = 0;
    lastMusicTime = currentTime;
    if (balancing_melody[lastMusicTone] == 0){
      return;
    }
    tone(PIN_BUZZER, balancing_melody[lastMusicTone], balancing_melody[lastMusicTone+1]);
    return;
  }

  if (currentTime-lastMusicTime < balancing_melody[lastMusicTone+1]){
    return;   
  }

  if (currentTime-lastMusicTime >= balancing_melody[lastMusicTone+1]){
    if (currentTime-lastMusicTime > balancing_melody[lastMusicTone+1] + balancing_melody[lastMusicTone+2]){
      lastMusicTone += 3;
      if (lastMusicTone < balancing_melody_size){
        lastMusicTime = currentTime;
        if (balancing_melody[lastMusicTone] == 0){
          return;
        }
        tone(PIN_BUZZER, balancing_melody[lastMusicTone], balancing_melody[lastMusicTone+1]);
      }
    }
    return;
  }
}
